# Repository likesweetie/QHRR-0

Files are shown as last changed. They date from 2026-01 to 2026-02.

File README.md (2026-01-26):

# !!직접 main 브랜치에 작업하지 않습니다!! 
## 아래 과정에서 에러난다고 GPT한테 물어봐서 Reset / Force Push같은거 하면 넌 뒤짐
잔디에 에러 스샷 올려서 같이 고민하기

### 작업 → Commit → Push 순서

1. 코드 수정 or 파일추가

2. GitHub Desktop에서 변경 사항 확인

3. Summary에 작업 내용 요약 작성

4. Commit to [branch 이름] (없으면 적당히 branch 생성)

5. Push origin

6. Push 후 GitHub 웹 페이지에서 Pull Request(PR) 생성 -> 관리자가 리뷰 승인 후 병합

### 사전설정

#### GitHub Desktop 설치 및 초기세팅

1. 아래 공식 링크에서 GitHub Desktop을 다운로드합니다.
👉 https://desktop.github.com/

2. 설치 후 실행합니다.

3. 실행 시 GitHub 로그인을 요청하면 본인의 GitHub 계정으로 로그인합니다

4. GitHub Desktop 실행

5. 상단 메뉴에서 File → Clone repository…

6. URL 탭 선택, 저장소 주소 입력

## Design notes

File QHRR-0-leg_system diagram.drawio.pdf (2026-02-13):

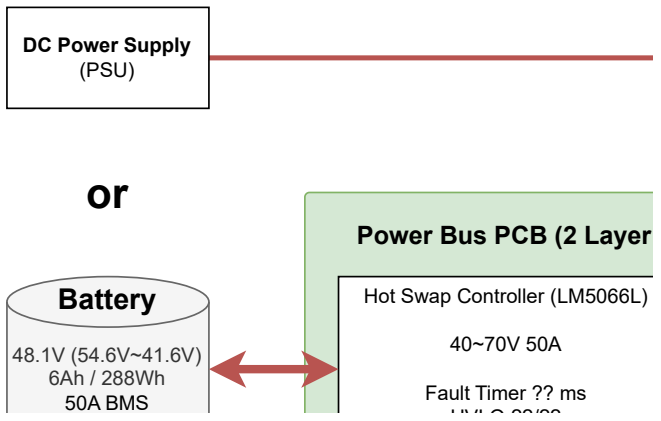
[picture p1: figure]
48.1V (54.6V~41.6V) 6Ah / 288Wh 50A BMS; Hot Swap Controller (LM5066L); Fault Timer ?? ms UVLO ??/??; Battery; Power Bus PCB (2 Layer; DC Power Supply (PSU)

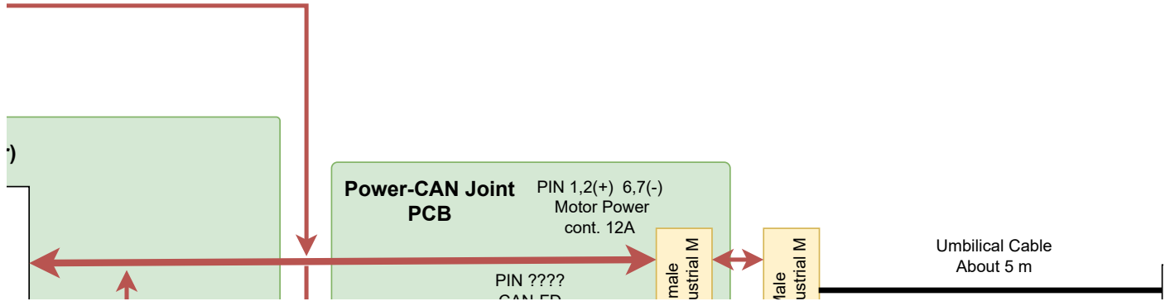
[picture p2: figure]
ustrial M; Male; male; PIN 1,2(+) 6,7(-) Motor Power cont. 12A; PIN ???? CAN FD; Power-CAN Joint PCB; Umbilical Cable About 5 m
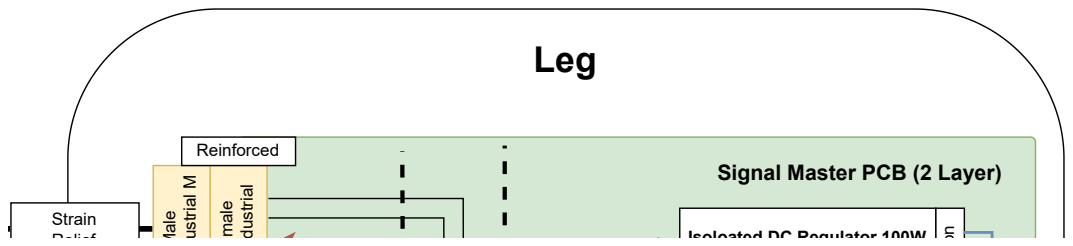
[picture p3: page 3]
Leg; male; dustrial; ustrial M; Male; Reinforced; Strain Relief

Signal Master PCB (2 Layer)

Isoloated DC Regulator 100W

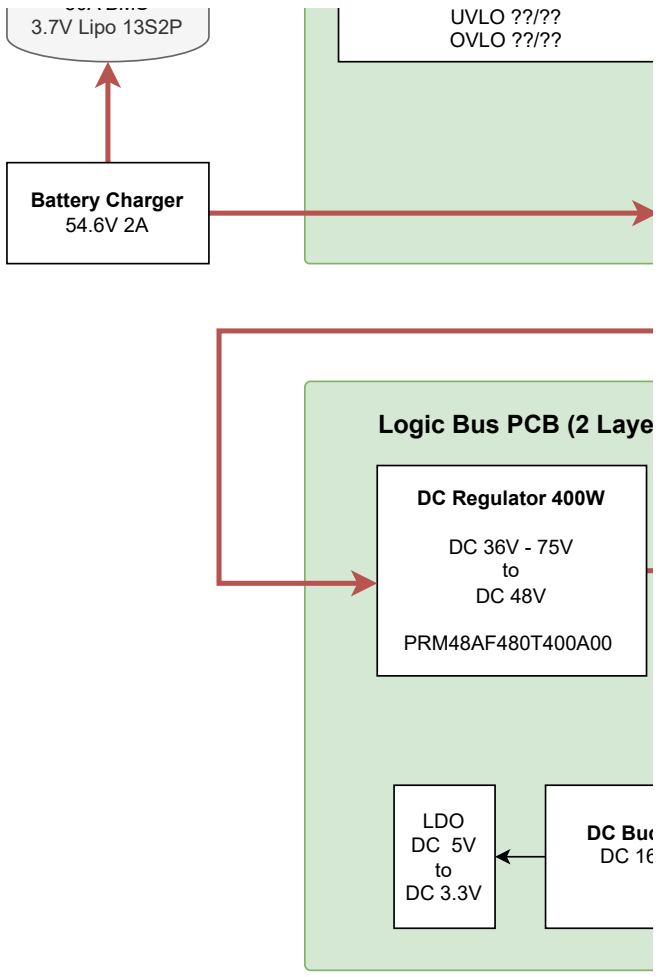
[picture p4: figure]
50A BMS 3.7V Lipo 13S2P; DC Regulator 400W; PRM48AF480T400A00; UVLO ??/?? OVLO ??/??; Battery Charger 54.6V 2A; Logic Bus PCB (2 Laye; DC Buc DC 16; LDO DC 5V to DC 3.3V

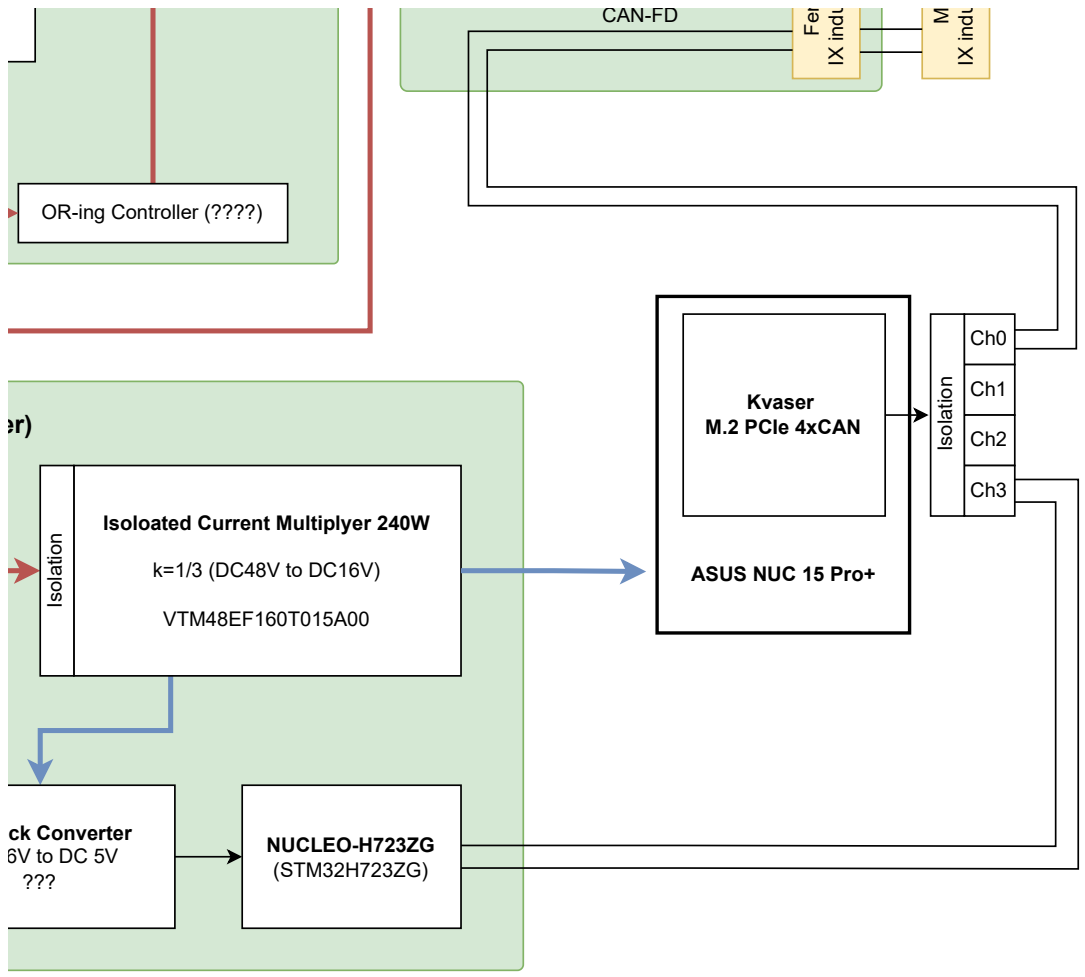
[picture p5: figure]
Isoloated Current Multiplyer 240W; VTM48EF160T015A00; NUCLEO-H723ZG (STM32H723ZG); OR-ing Controller (????) Isolation; IX indu; Fem; CAN-FD; ASUS NUC 15 Pro+; Isolation; Kvaser M.2 PCIe 4xCAN; ck Converter 6V to DC 5V ???
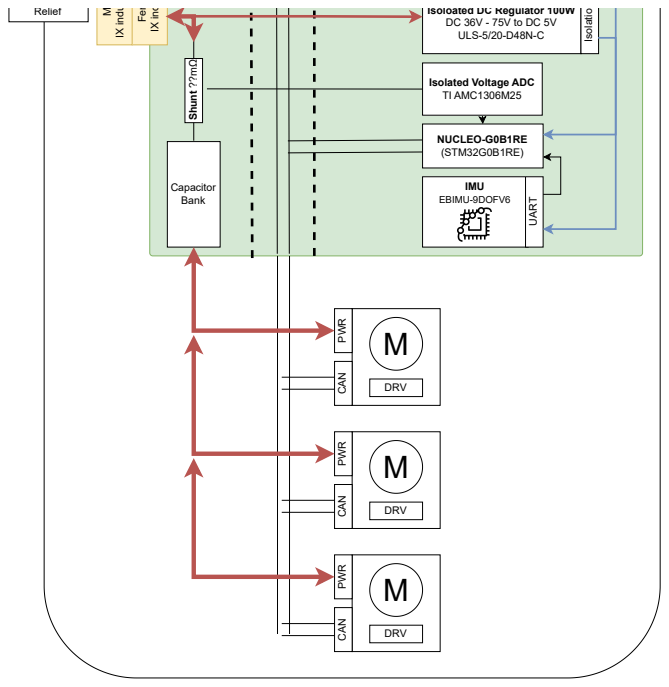
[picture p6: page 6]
DRV; CAN; NUCLEO-G0B1RE (STM32G0B1RE); IMU EBIMU-9DOFV6; UAR; Capacitor Bank; IX ind; Fem; Isolatio; Shunt ??mΩ; IX indu; Relief

Isoloated DC Regulator 100W
ULS-5/20-D48N-C

Isolated Voltage ADC
TI AMC1306M25

PWR CAN PWR CAN PWR

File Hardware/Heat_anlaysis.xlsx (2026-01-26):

 | Stack | 두께 m | 접촉면적 m^2 | 열저항 | 열전도율 W/(m·K) | 발열(W)
Ambient Temp. (C)
30
Max surface Temp
50 | 알루미늄 7075 외피(Fin) | 0.005 |  | 0.0078125 | 128 | 0
 | 알루미늄 7075 외피(구조물) | 0.005 |  | 0.0078125 | 128 | 0
 | 서멀그리스 |  |  | 0.125 | 8 | 0
 | 구리 T2 Heat Sink | 0.01 |  | 0.002493765586 | 401 | 0
 | 서멀그리스 |  |  | 0.125 | 8 | 0
 | CPU (cTDP / 기본65W) |  |  |  |  | 65

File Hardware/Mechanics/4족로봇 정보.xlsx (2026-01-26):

 | standing 크기 | 무게 | 가반하중 | 최대속도 |  | Thigh | calf
RBQ10 | 945 X 440 X 565mm | 37kg | 10kg | 7.2km/h | 2m/s | 1.8kg | 0.45kg
B2 | 1098 X 450 X 645 mm | 60kg | 120kg | 21.6km/h | 6m/s | 4.536kg | 0.404kg
spot | 1100 X 500 X 610 mm | 32.7kg | ? | 5.76km/h | 1.6m/s | 2.256kg | 0.330kg
Black panther 2 | ? X ? X 630 mm | 38kg | ? | 36km/h | 10m/s
ANYmal | 930 X 530 X 890 mm | 50kg | 15kg | 4.69km/h | 1.30m/s
Ghost Robotics vision 60 | ? X ? X ? Mm | 51kg | 10kg | 10.8km/h | 3m/s | 1.2kg | 0.38kg
 |  |  |  |  |  |  |  | hip
 |  |  |  |  |  |  |  | 2.75kg

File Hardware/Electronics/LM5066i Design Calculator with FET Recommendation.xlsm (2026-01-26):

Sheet: Instructions
 |  |  |  |  | © 2014
 | LM5066/I Design Tool with FET Recommendation - Rev. A
 | Typical design procedure
 | Before proceeding, please go through the application note |  |  | Robust Hot Swap Design (https://www.ti.com/lit/an/slva673a/slva673a.pdf)
 | and the design example in the |  | LM5066I Datasheet (See "Applications and Implementation") (https://www.ti.com/lit/ds/symlink/lm5066i.pdf)
Step 1: | 1. Enter your system parameters (operating voltage limits, load current, load capacitance, system max ambient temperature )
 | 2. Enter FET operating parameters (preferred FET operating junction temperature, thermal impedance)
 |  | Note: The tool adjusts the number of FETs required in parallel to maintain the preferred FET operating junction temperature.
 |  | Note: Thermal impedance is heavily dependent on the board layout and the amount of copper connected to the drain of the FET.
 |  | Thermal impedance is required to determine MOSFET SOA margin.
 | 3. Enter the load startup conditions (startup mode, startup load type, load turn on threshold, startup load value)
Step 2: | 1. Set the current limit settings. Use a resistive divider to reduce effective sense resistance if needed.
 | 2. Select Target power limit greater than the Minimum Recommended Power Limit threshold
Step 3: | 1. Select MOSFETs from the dropdown menu.
 | 2. Compare their SOA margin, cost, power dissipation at full load and number of FETs required in parallel to know which FET fits your design perfectly.
 |  | Note: You can also enter the SOA data of a non-TI FET to compare it with TI FETs.
 |  | An SOA margin greater than 1.1 is required and greater than 1.3 is recommended for safe operation
 | 3. If none of the FETs satisfy the SOA margin, try to change the following parameters:
 |  | a. In case of power limit startup mode, reduce the load startup conditions or use a different FET in the non-TI FET column.
 |  | b. In case of soft start startup mode, reduce the fault timer or use a different FET in the non-TI FET column.
 | Note: The FETs selected in this section will be available as the final choices in the next section.
 | (Links to the TI FET product pages have been provided)
Step 4: | 1. Select an FET from the dropdown menu.
 | 2. Review start up conditions to check whether selected FET is operating with reasonable margin, within the SOA curve.
 | 3. Adjust Soft-start and Timer capacitances to get accurate SOA measurements.
Step 5: | 1. Enter desired UVLO and OVLO threshold values to get recommended resistor values.
 | 2. In case any of the cells in the threshold table is highlighted in red, adjust the resistor values.
 | 3. If nearest resistor values still give red highlighted cells, change the configuration
Step 6: | Done. View the design summary with all the results
 | * Comments on the data to be filled/expected are provided to guide you
 | Notes
 | 1. This worksheet is designed for use with Microsoft Excel 5.0 or later. Its use is intended to assist power supply designers in their
 | routine, day-to-day calculations.
 | 2. All worksheets have light green inputs cells, white calculated cells, yellow warning cells and red high-risk cells.
 | 3. Formulas and device constants used in the spreadsheet are locked to prohibit them from accidentally being overwritten or deleted.
 | TEXAS INSTRUMENTS TEXT FILE LICENSE Copyright (c) 2014 Texas Instruments Incorporated All rights reserved not granted herein. Limited License. Texas Instruments Incorporated grants a world-wide, royalty-free, non-exclusive license under copyrights and patents it now or hereafter owns or controls to make, have made, use, import, offer to sell and sell ("Utilize") this software subject to the terms herein. With respect to the foregoing patent license, such license is granted solely to the extent that any such patent is necessary to Utilize the software alone. The patent license shall not apply to any combinations which include this software, other than combinations with devices manufactured by or for TI (“TI Devices”). No hardware patent is licensed hereunder. Redistributions must preserve existing copyright notices and reproduce this license (including the above copyright notice and the disclaimer and (if applicable) source code license limitations below) in the documentation and/or other materials provided with the distribution Redistribution and use in binary form, without modification, are permitted provided that the following conditions are met: * No reverse engineering, decompilation, or disassembly of this software is permitted with respect to any software provided in binary form. * any redistribution and use are licensed by TI for use only with TI Devices. * Nothing shall obligate TI to provide you with source code for the software licensed and provided to you in obje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

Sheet: Design Calculator
LM5066/I PMBus Hot Swap Design Tool with FET Recommendation
 | www.ti.com/hotswap
 |  |  | Enter Values in Green Shaded Cells
 |  |  | Calculated Values are shown in White Cells
 |  |  | Yellow and Red cells highlight potential issues with the design. Red highlights items that are higher risk.
 |  |  | LM5066I Datasheet (http://www.ti.com/product/lm5066i)
 |  |  | *For additional questions not addressed in the instructions, please post on E2E.ti.com
 | Step 1: System Parameters |  |  | Minimum Input Operating Voltage: VIN(MIN) | 40 | V
 |  |  |  | Nominal Input Operating Voltage: VIN(NOM) | 48 | V
 |  |  |  | Maximum Input Operating Voltage: VIN(MAX) | 70 | V
 |  |  |  | Maximum Load Current: IOUT(MAX) | 50 | A
 |  |  |  | Maximum Output Load Capacitance: CLOAD | 220000 | µF
 |  |  |  | Maximum Ambient Operating Temperature: TMAX | 50 | oC | Note: The tool adjusts the number of FETs required in parallel to maintain the preferred FET operating junction temperature (TJ,DC)
 |  |  |  | Preferred FET Operating Junction Temperature (TJ,DC) | 80
 |  |  |  | Estimated MOSFET RQJA | 100
 |  |  |  | Load Turn-On Threshold | 40 | V
 |  |  |  | Startup Load Type | Constant Current |  | Note: In case none of the FETs satisfy the SOA margin, reduce the load startup conditions
 |  |  |  | Startup Load Value | 10 | A
 |  |  |  | System start-up mode | Soft Start |  | Note: In case none of the FETs satisfy the SOA margin, reduce the fault timer
 |  |  |  | Fault timer required | 0.050 | ms
 | Step 2: Current Limit and Power Limit Selection |  |  | Current Limit Range (CL) | 26 mV
 |  |  |  | Maximum Recommended Value for Effective Sense Resistance | 0.46 | mW
 |  |  |  | Use External Resistor Divider to Reduce Effecitve RS | No
 |  |  |  | Enter the Resistance for RS | 0.1 | mW
 |  |  |  | Recommended Value for RCL1 | NA | W
 |  |  |  | Recommended Value for RCL2 | NA | W
 |  |  |  | Enter value for RCL1 | 10 | W
 |  |  |  | Enter value for RCL2 | 2.8 | W
 |  |  |  | Effective Sense Resistance (RS,EFF) | 0.10 | mW
 |  |  |  | Resulting Minimum Current Limit | 234.0 | A
 |  |  |  | Resulting Typical Current Limit | 260.0 | A
 |  |  |  | Resulting Maximum Current Limit | 286.0 | A
 |  |  |  | Maximum Power Dissipation in RS | 8.2 | W
 |  |  |  | Fault Response | Latch Off |  |  |  |  |  | Note: Use a resistive divider to fine tune the current limit setting if needed
 |  |  |  | Circuit Breaker to Current Limit Raitio | 1.9 x Current Limit
 |  |  |  | Minimum Power Limit to Ensure Vsns > 4mV (PLIM,MIN) | 2800.0 | W
 |  |  |  | Target Power Limit | 3000.00 | W
 |  |  |  | Calculated RPWR | 36.71 | kW
 |  |  |  | Actual RPWR | 47 | kW
 |  |  |  | Actual PLIM | 3720.00 | W
 | Step 3: MOSFET Suggestions |  |  | Q1 FET Name | Part Number , SOA margin , $1ku | Part Number , SOA margin , $1ku | MOSFET from Non-TI Suppliers
 | Scroll down the dropdown menu to select MOSFET |  |  | Choose FETs for comparison | CSD19536KTT , 1.23 , $1.972 | CSD19535KTT , 1.16 , $1.313 | Non-TI MOSFET
 |  |  |  | MOSFET On resistance @ TJ,DC | 3.144 | 4.794 | 2.000
 |  |  |  | Maximum FET Junction Temperature | 175 | 175 | 175 | mW
 |  |  |  | 10ms SOA Current@ VIN(MAX) | 400.00 | 400.00 | 400.00 | oC
 |  |  |  | 100µs SOA Current @ VIN(MAX) | 102.96 | 37.38 | 100.00 | A
 |  |  |  | 1ms SOA Current @ VIN(MAX) | 9.39 | 4.99 | 20.00 | A
 |  |  |  | 10ms Current at @ VIN(MAX) | 2.92 | 1.49 | 5.00 | A
 |  |  |  | 100ms SOA Current at @ VIN(MAX) | 1.49 | 0.87 | 1.00 | A
 |  |  |  |  |  |  |  | A
 | Note: TI recommends choosing a FET with SOA current specified for 100ms and/or 1s or DC. If choosing a FET without these parameters, this calculator will estimate the values via extrapolation, which leaves an inherent associated risk. |  |  | Number of FETs suggested | 6 | 7 | 5
 |  |  |  | FET Power dissapation at full load (per FET) | 0.22 | 0.24 | 0.20 | #
 |  |  |  | Maximum steady state FET Junction Temperature (TJ,DC) | 71.83 | 74.46 | 70.00 | W
 |  |  |  | SOA Margin | 2.01 | 0.96 | 2.00 | oC
 |  |  |  | Webpage Link | CSD19536KTT | CSD19535KTT | Enter Webpage Link
 |  |  |  | Cost per FET (1k USD) | $1.972 | $1.313 | Enter Cost Details |  |  | Note: Hover here to see the 3 values affecting this curve, consult a thermal expert if you are unsure!
 |  |  |  | Total Cost of the FETs | $11.832 | $9.191
 |  |  |  |  | Note: If none of the FETs are meeting the requirement, reduce the startup load or select a stronger FET in cell H54
 |  |  |  |  | Note: If none of the FETs are meeting the requirement, reduce the fault timer or select a stronger FET in cell H54
 | Step 4: Startup |  |  | Select preferred FET from the dropdown menu | CSD19536KTT , 2.63 , $1.972
 |  |  |  | Timer Overview
 |  |  |  | Typical Start Time with Vinmax (Tstart) | 350.00 | ms
 |  |  |  | IFET - ILOAD margin (lowest for Vout range) | 81.48148148%
 |  |  |  | Target Fault Timer: Tstart + Margin | 525.00 | ms
 |  |  |  | Target Timer capacitance | 10096.15 | nF
 |  |  |  | Selected Timer capacitance | 100 | nF
 |  |  |  | Final Fault Timer(Tfault) | 5.20 | ms
 |  |  |  | Derated SOA / PLIM | #N/A
 |  |  |  | Can a "hot" board be hotplugged | No
 |  |  |  | Recommended slew Rate (max) | #N/A | V/ms
 | Note: This is the typical dv/dt rate, but max value can be 2x. This is because the gate source current can vary from 20uA to 40uA. Thus TI recommends keeping the overall SOA margin during start-up >1.5 in order to compensate for this. |  |  | Recommended slew Rate (min) | #N/A | V/ms
 |  |  |  | dv/dt rate on Vout | 0.2 | V/ms
 |  |  |  | calculated SS capacitance | 100.00 | nF
 |  |  |  | actual SS capacitance | 100 | nF
 |  |  |  | actual typical dv/dt rate on Vout | 0.20 | V/ms
 |  |  |  | SOA margin during start-up | #N/A
 |  |  |  | Target Fault Time | 0.01 | ms
 |  |  |  | Calculated Timer Capacitance | 0.19 | nF
 |  |  |  | Actual Timer Capacitance ( pick one smaller than CT,CALC) | 4.7 | nF
 |  |  |  | Actual Fault Time (Tfault) | 0.24 | ms
 |  |  |  | SOA margin during "hot-short" or "start-into short" | #N/A
 |  |  |  | Resulting Typical Insertion Delay Time | 3.81875 | ms
 |  |  |  | Resulting Typical Restart Time | 38.95 | ms
 | Step 5: UVLO, OVLO & PGD Thresholds |  |  | Select Option A or Option B | Option B
 |  |  |  | Desired Upper UVLO Threshold | 38 | V
 |  |  |  | Desired Lower UVLO Threshold | 35 | V
 |  |  |  | Desired Upper OVLO Threshold | 65 | V
 |  |  |  | Desired Lower OVLO Threshold | 63 | V
 |  |  |  | Recommended Resistance for: R1 | 150.00 | kW
 |  |  |  | R2 | 11.44 | kW
 |  |  |  | R3 | 95.24 | kW
 |  |  |  | R4 | 3.75 | kW
 |  |  |  | Enter the Resistance for R1 | 150 | kW
 |  |  |  | Enter the Resistance for R2 | 11.5 | kW
 |  |  |  | Enter the Resistance for R3 | 95.3 | kW
 |  |  |  | Enter the Resistance for R4 | 3.74 | kW
 |  | Resulting Thresholds: | Minimum | Typical | Maximum
 |  | Resulting Upper UVLO Threshold = | 36.24 | 37.83 | 39.41 | V
 |  | Resulting Lower UVLO Threshold = | 33.84 | 34.83 | 35.81 | V
 |  | Resulting Upper OVLO Threshold = | 63.29 | 65.14 | 67.00 | V
 |  | Resulting Lower OVLO Threshold = | 61.00 | 63.14 | 65.47 | V
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

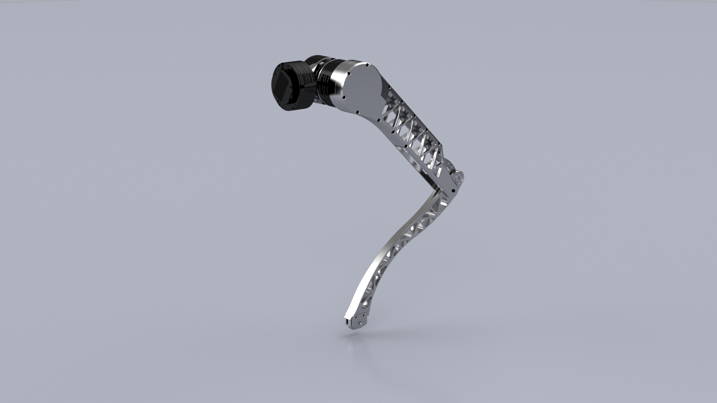
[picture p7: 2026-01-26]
Hardware/Mechanics/Untitled Project.jpg

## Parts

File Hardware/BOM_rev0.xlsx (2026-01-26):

 |  |  |  |  |  |  |  |  |  |  | 총액 | ₩4096015
 |  |  |  |  |  |  |  |  |  |  | 1순위 총액 | ₩3685553
Part Number | Rev | Class | Type | Retail | Priority | Part Name | Part Description | Qty. | Spec / Model | Manufacturer | Supplier | Price/Qty | Price | 서류처리? | 구매? | 구분
 | 0 | Electronics | Component | TRUE | 1 | ASUS NUC 15 Pro+ NUC15CRSU9 (베어본) | Control PC | 1 |  | ASUS |  | ₩1400000 | ₩1400000 | 구매기안중 |  | SPG RISE 재료비
 | 0 | Electronics | Component | TRUE | 1 | 삼성전자 노트북 램 DDR5- 32GB | Control PC | 1 |  | 삼성전자 |  | ₩350000 | ₩350000 | 구매기안중 |  | SPG RISE 재료비
 | 0 | Electronics | Component | TRUE | 1 | m.2 SSD 1TB 2280 | Control PC | 1 |  | 하이닉스 |  | ₩400000 | ₩400000 | 구매기안중 |  | SPG RISE 재료비
 | 0 | Electronics | Component | TRUE | 1 | Kvaser M.2 PCIe 4xCAN | CAN | 1 |  | KVASER |  | ₩770000 | ₩770000 | 구매기안중 |  | SPG RISE 재료비
 |  | Electronics | Component | TRUE | 1 | EBIMU-9DOFV6 | IMU | 1 |  | 이투박스 | 디바이스마트 | ₩173800 | ₩173800 |  |  | SPG RISE 재료비
 |  | Electronics | Component | TRUE | 1 | NUCLEO-G0B1RE | MCU | 1 |  | STMicroelectronics | 디바이스마트 | ₩21230 | ₩21230 |  |  | SPG RISE 재료비
 |  | Electronics | Component | TRUE | 1 | ULS-5/20-D48N-C | DC/DC 컨버터 | 1 |  |  | 디바이스마트 | ₩77539 | ₩77539 |  |  | SPG RISE 재료비
 |  | Electronics | Component | TRUE | 1 | PVHC7F23SS644 SWITCH PUSHBUTTON SPST 20A 250V | 전원스위치 | 1 | 20A 250V | E-Switch | 디바이스마트 | ₩47652 | ₩47652 |  |  | SPG RISE 재료비
 |  | Electronics | Component | TRUE | 1 | AMC1306M25QDWVRQ1 | ADC 컨버터 | 5 |  | Murata Power | 디바이스마트 | ₩10593 | ₩52965 |  |  | SPG RISE 재료비
 |  | Electronics | Component | TRUE | 1 | WSLP59311L000FEB 션트저항 1m옴 | 션트저항 | 2 |  | Vishay Dale | 디바이스마트 | ₩5731 | ₩11462
 |  | Electronics | Component | TRUE | 1 | WSLP5931L1000FEA 션트저항 0.1m옴 | 션트저항 | 2 |  | Vishay Dale | 디바이스마트 | ₩6347 | ₩12694 |  |  | SPG RISE 재료비
 |  | Electronics | Component | TRUE | 1 | B380-13-F | 쇼트키 다이오드 | 5 |  | Diodes Incorporated | 디바이스마트 | ₩1595 | ₩7975 |  |  | SPG RISE 재료비
 |  | Electronics | Component | TRUE | 1 | 1N4148W-7-F | 스위칭다이오드 | 10 |  | Diodes Incorporated | 디바이스마트 | ₩198 | ₩1980 |  |  | SPG RISE 재료비
 |  | Electronics | Component | TRUE | 1 | CSD19536KTT | 배터리 전원 FET | 10 |  | TI | 디바이스마트 | ₩9922 | ₩99220 |  |  | SPG RISE 재료비
 |  | Electronics | Component | TRUE | 1 | MMBT3904 | BJT TR | 20 |  | Diotec Semiconductor | 디바이스마트 | ₩187 | ₩3740 |  |  | SPG RISE 재료비
 |  | Electronics | Component | TRUE | 1 | 5.0SMDJ43CAS | ESD 다이오드 69.4VC | 10 |  | Littelfuse Inc. | 디바이스마트 | ₩3938 | ₩39380 |  |  | SPG RISE 재료비
 |  | Electronics | Component | TRUE | 1 | SSW-138-01-T-S | 신호 커넥터 | 4 |  | Samtec | 디바이스마트 | ₩5742 | ₩22968 |  |  | SPG RISE 재료비
 |  | Electronics | Component | TRUE | 1 | XT60PW-M | 전원 커넥터 | 10 |  | Changzhou Amass Elec | 디바이스마트 | ₩1089 | ₩10890 |  |  | SPG RISE 재료비
 |  | Electronics | Component | TRUE | 1 | Male 플러그 4핀 [LP-16-C04PE-02-001] | 전원 커넥터 | 4 |  | crinco | 디바이스마트 | ₩7040 | ₩28160 |  |  | SPG RISE 재료비
 |  | Electronics | Component | TRUE | 1 | Female 원형 소켓 4핀 [LP-16-J04SX-02-101] | 전원 커넥터 | 4 |  | crinco | 디바이스마트 | ₩5280 | ₩21120 |  |  | SPG RISE 재료비
 |  | Electronics | Component | TRUE | 1 | 2311765-1 | 신호 커넥터 | 2 |  | TE Connectivity | 디바이스마트 | ₩4169 | ₩8338
 |  | Electronics | Component | TRUE | 2 | PRM48AF480T400A00 | DC/DC 컨버터 | 1 |  | Vicor | 디바이스마트 | ₩226072 | ₩226072 |  |  | SPG RISE 재료비
 |  | Electronics | Component | TRUE | 2 | VTM48EF160T015A00 | DC/DC 컨버터 | 1 |  | Vicor | 디바이스마트 | ₩130520 | ₩130520
 |  | Electronics | Component | TRUE | 2 | NUCLEO-H723ZG | MCU | 1 |  | STMicroelectronics | 디바이스마트 | ₩53870 | ₩53870
 |  | Mechanical | Component | TRUE | 1 | C-NUHFN160 | 손잡이 | 5 |  |  | 미스미 | ₩8888 | ₩44440 |  |  | 태성 RISE 재료비
 |  | Mechanical | Component | TRUE | 1 | 쉬멕스 풀림방지 볼트 M3 50pcs | 볼트 | 1 |  | 쉬멕스 | 쉬멕스 | ₩40000 | ₩40000
 |  | Mechanical | Component | TRUE | 1 | 쉬멕스 풀림방지 볼트 M4 50pcs | 볼트 | 1 |  | 쉬멕스 | 쉬멕스 | ₩40000 | ₩40000
 |  | Mechanical | Component | TRUE | 1 | 핀 | 위치 핀 | 10 |  | 미스미 | 미스미
 |  |  |  |  |  |  |  |  |  |  |  |  | ₩0
 |  |  |  |  |  | 각종 FC에 사용하는 GH1.25 |  |  |  |  |  |  | ₩0
 |  |  |  |  |  |  |  |  |  |  |  |  | ₩0
 |  |  |  |  |  |  |  |  |  |  |  |  | ₩0
 |  | Software
S-01 | 0 | SQLite
 |  | OpenBOM
 |  | WireViz
 |  | ZeroMQ |  |  |  | 원격 메시징 라이브러리 |  |  |  | JCL PCB
 |  | googletest
 |  |  |  | FALSE |  | Heat Sink

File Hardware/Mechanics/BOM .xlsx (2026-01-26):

 |  |  |  |  | (단위 : 천원)
 | 구매처 | 품번/이름 | 수량 | 재료 | 업체명 : 유일 | 엠더블유에스 | GP KOREA | 지엔피
가공 부품 |  | calf_link_I | 1 | S45C | 120 | 95 | 60 | 30
 |  | calf_link_II | 1 | S45C | 150 | 75 | 60 | 30
 |  | calf_thigh_I | 1 | S45C | 80 | 70 | 60 | 35
 |  | connector_1 | 1 | 6061-T6 | 80 | 80 | 80 | 55
 |  | connector_2 | 1 | 6061-T6 | 90 | 90 | 80 | 60
 |  | foot_cover_1 | 1 | 6061-T6 | 50 | 120 | 60 | 40
 |  | foot_cover_2 | 1 | 6061-T6 | 50 | 120 | 60 | 40
 |  | hip_calf_jig | 1 | 6061-T6 | 180 | 420 | 150 | 90
 |  | hip_stopper | 1 | 7075-T6 | 220 | 180 | 120 | 45
 |  | hip_thigh_2 | 1 | 6061-T6 | 350 | 500 | 200 | 150
 |  | link | 1 | S45C | 400 | 260 | 250 | 250
 |  | shaft_1 | 1 | S45C | 120 | 85 | 60 | 40
 |  | shaft_2 | 1 | S45C | 200 | 80 | 80 | 60
 |  | thigh(1)-2 | 1 | 6061-T6 | 350 | 580 | 550 | 350
 |  | thigh(2)-2 | 1 | 6061-T6 | 350 | 580 | 550 | 350
 |  | thigh_stopper | 1 | 7075-T6 | 150 | 150 | 100 | 45
 |  | spacer_3.5 | 2 | 6061-T6 | 80 | 50 | 120 | 40
 |  | calf | 1 | 7075-T6 | 400 | 650 | 450 | 320
 |  |  |  | 총 가격 : | 3420 | 4185 | 3090 | 2030
 |  |  |  | 세금 포함 | 약 3,760,000 | 약 4,603,000 | 약 3,399,000 | 약 2,233,000
베어링
 | NSK | 6900ZZ(C-E6900) | 2 |  | 내경 : 10 |  | 외경 : 22
볼트 | NSK | 6001ZZ(C-E6001) | 2 |  | 내경 : 12 |  | 외경 : 28
 | NTN | C-E678ZZ | 2 |  | 내경 : 6 |  | 외경 : 10
핀
스페이서 | 쉬멕스 | P00180-04-10 | 50 |  | M4 볼트 |  | 길이 10mm
 | 쉬멕스 | P00180-04-16 | 50 |  | M4 볼트 |  | 길이 16mm
 | 미스미 | E-FPDSC4-P3-L4-B4 | 7
 | 미스미 | CLBP12-16-10-UKC | 1 | 5000계 알루미늄 합금
 |  | CLBP10-13-3-UKC | 2 | 5000계 알루미늄 합금

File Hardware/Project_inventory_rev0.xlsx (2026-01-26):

Part Number | Rev | Part Name | Class | Part Description | Qty. | Spec / Model | Supplier | Price/Qty | Price
EL-01 | 1 | NUC | Electronics | Control PC

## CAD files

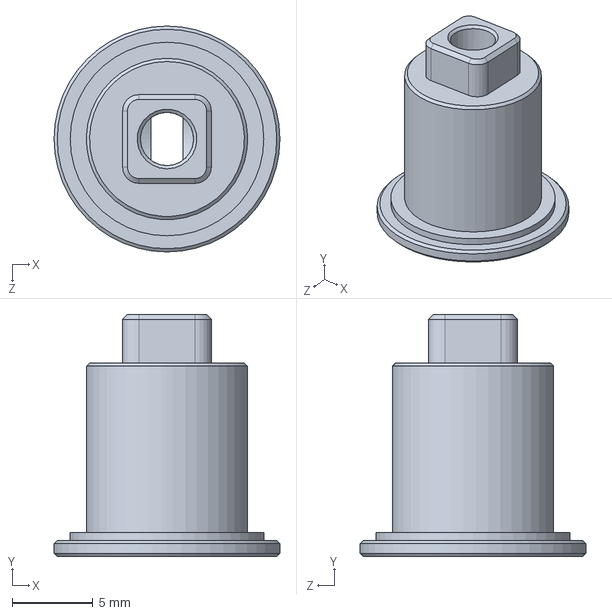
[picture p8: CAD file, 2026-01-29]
Hardware/Mechanics/4족 3D/calf_link_l.SLDPRT
14.0 x 15.0 x 14.0 mm

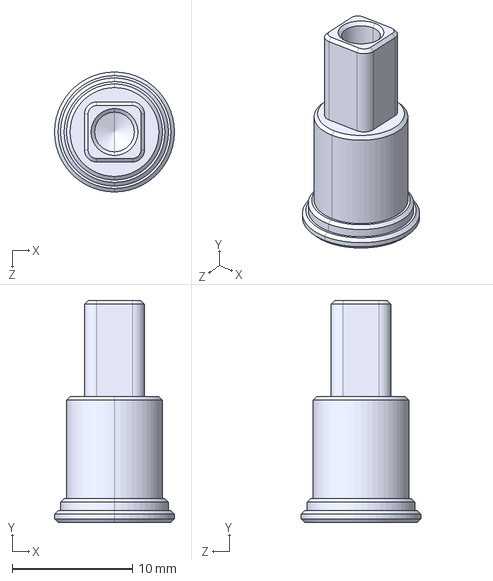
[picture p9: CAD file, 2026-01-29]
Hardware/Mechanics/4족 3D/STEP 파일/shaft_1.STEP
10.0 x 18.5 x 10.0 mm

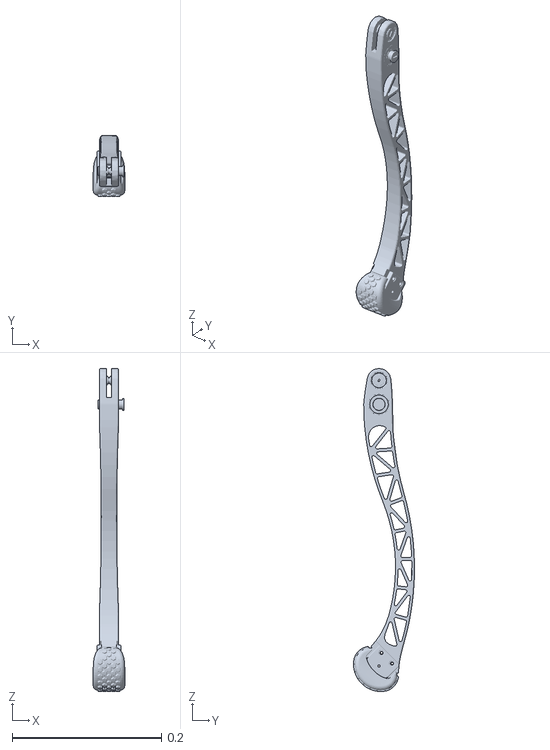
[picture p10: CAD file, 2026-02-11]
Hardware/Mechanics/4족 3D/URDF_14/meshes/Calf_link.STL
0.0423 x 0.0816 x 0.432

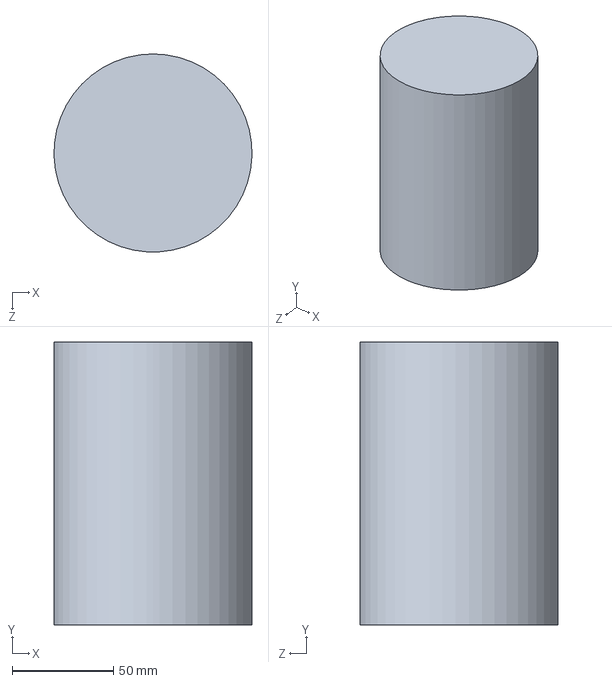
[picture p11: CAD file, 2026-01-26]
Hardware/Mechanics/시뮬/Thigh_calf_motor.SLDPRT
97.9 x 140.0 x 98.0 mm

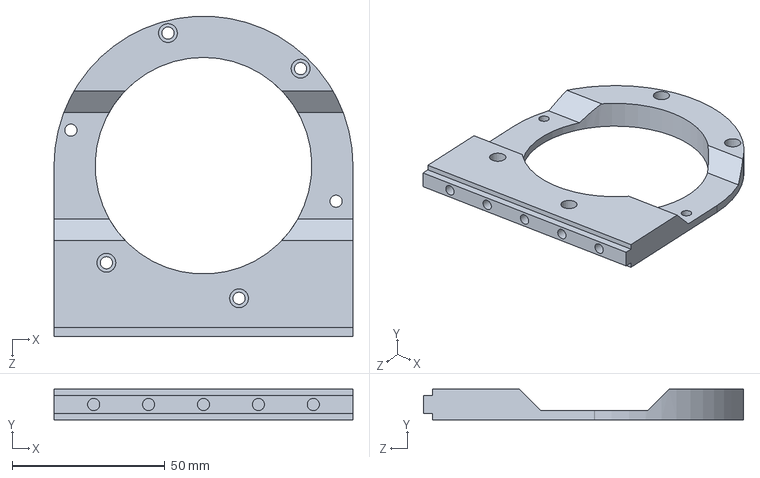
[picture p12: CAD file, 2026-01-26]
Hardware/Mechanics/안 쓰는 것/hip-thigh.SLDPRT
98.0 x 10.0 x 104.9 mm

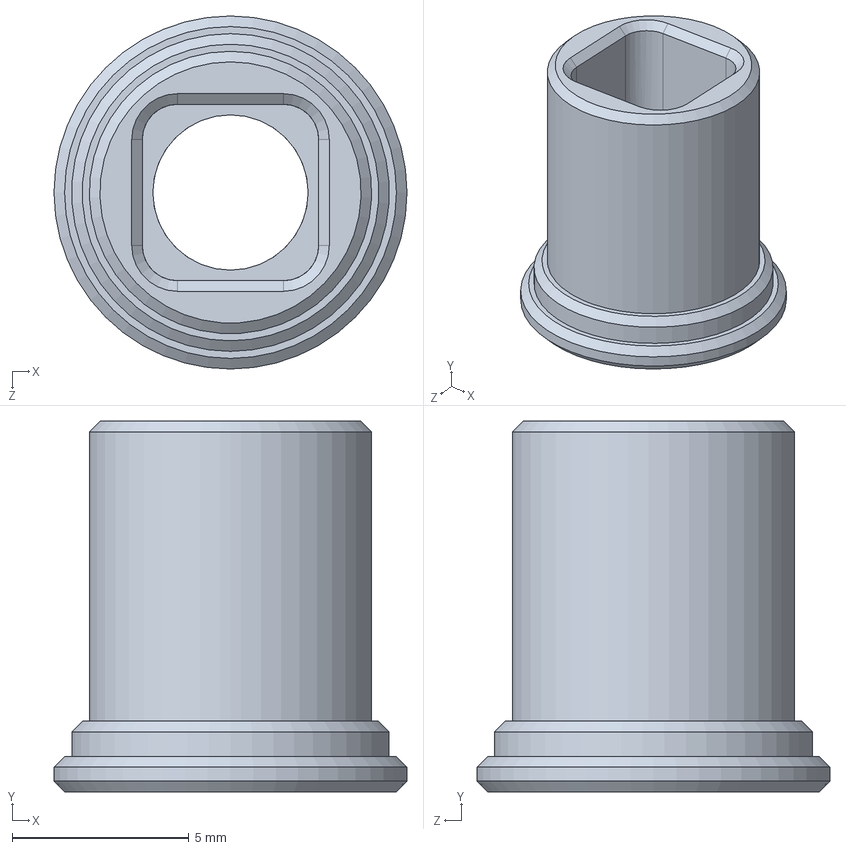
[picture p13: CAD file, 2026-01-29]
Hardware/Mechanics/4족 3D/shaft_2.SLDPRT
10.0 x 10.5 x 10.0 mm

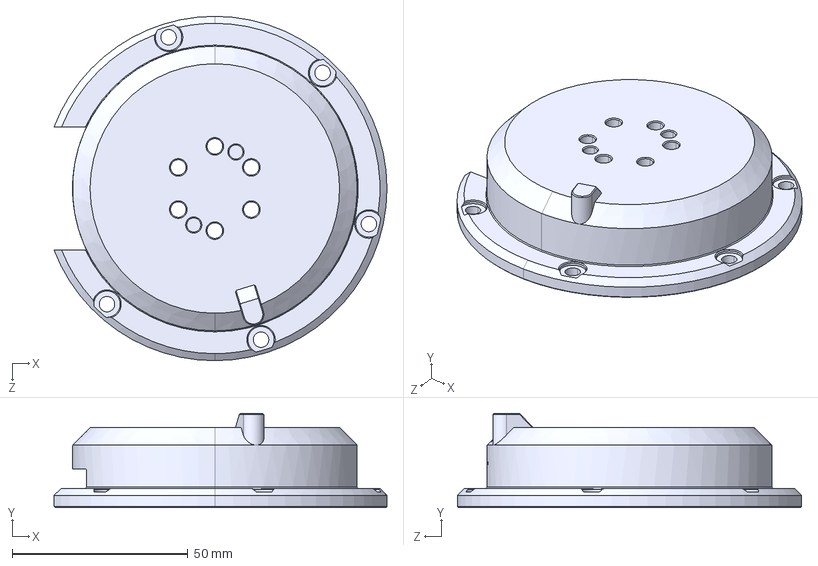
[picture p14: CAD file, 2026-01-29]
Hardware/Mechanics/4족 3D/STEP 파일/hip_calf_jig_2.STEP
94.8 x 26.8 x 98.0 mm

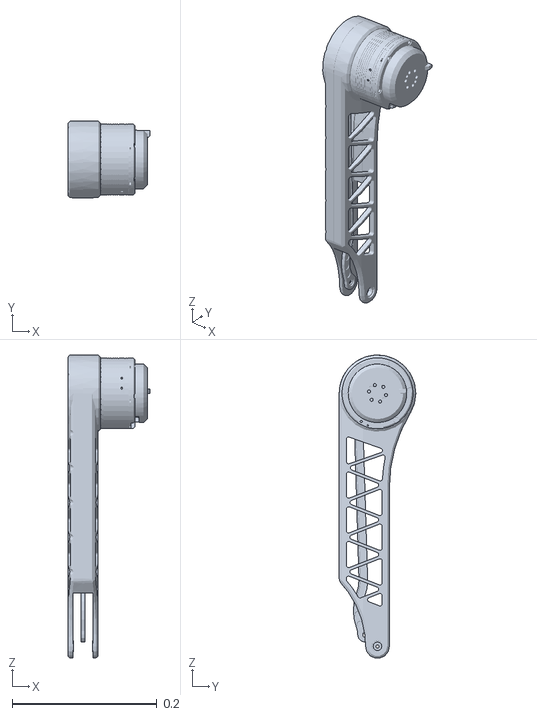
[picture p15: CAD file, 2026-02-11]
Hardware/Mechanics/4족 3D/URDF_14/meshes/Thigh_link.STL
0.114 x 0.106 x 0.419

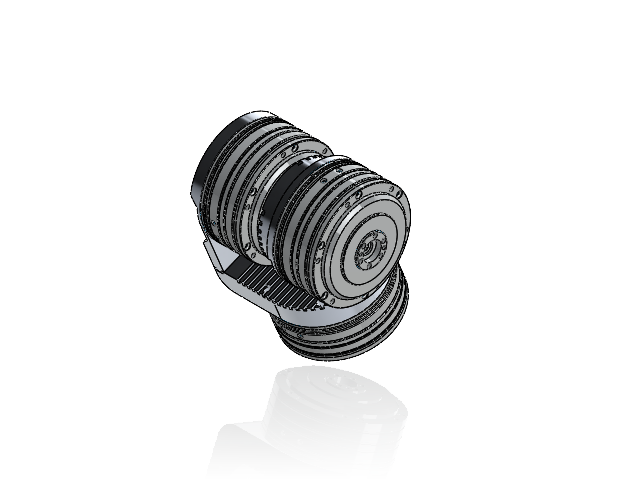
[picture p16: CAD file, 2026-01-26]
Hardware/Mechanics/안 쓰는 것/hip_thigh assembly.SLDASM
AK10-9 KV60 V3.0-3D.step x 3
hip_calf_jig
hip_jig
hip-thigh

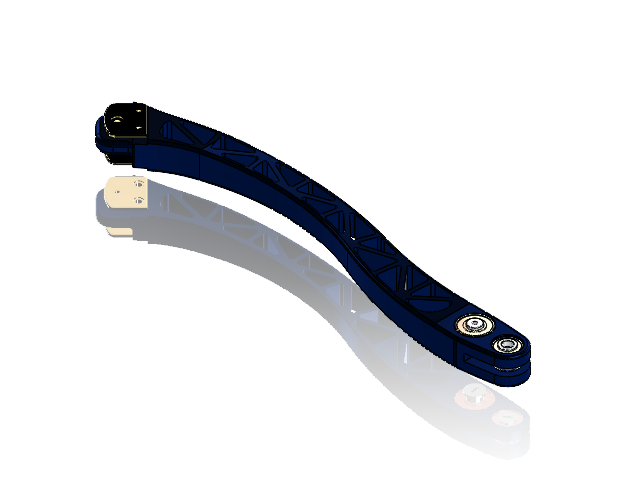
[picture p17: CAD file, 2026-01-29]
Hardware/Mechanics/4족 3D/Calf_link.SLDASM
B6001ZZ x 2
B6900ZZ x 2
calf_link_l
calf_link_ll
calf_thigh_I
calf-1
foot_cover_1
foot_cover_2
CLBP10-13-3-UKC x 2
CLBP12-16-10-UKC

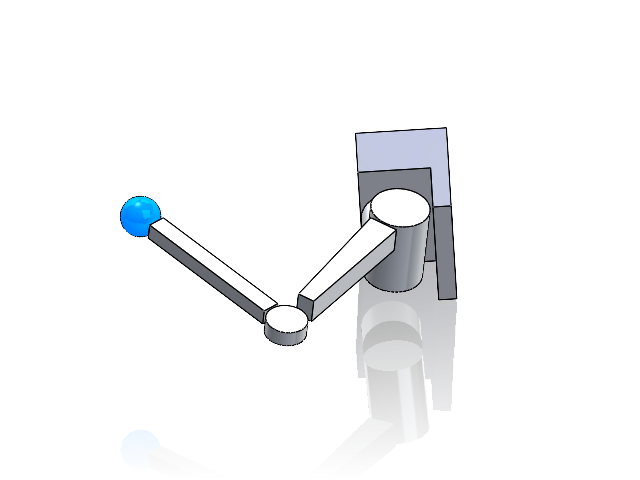
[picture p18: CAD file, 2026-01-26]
Hardware/Mechanics/시뮬/어셈블리.SLDASM
Calf_mesh
foot_mesh
Hip_motor
Thigh_calf_motor
Thigh_mesh
knee_joint
platform

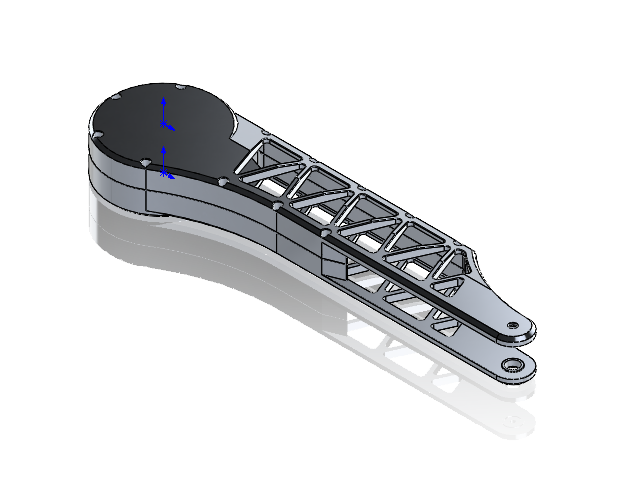
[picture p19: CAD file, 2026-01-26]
Hardware/Mechanics/4족 3D/허벅지 일체형.SLDASM
thigh(1) - 2
thigh(2) - 2

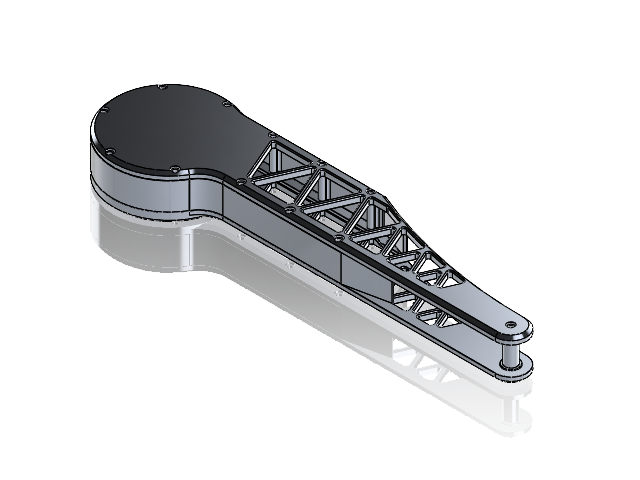
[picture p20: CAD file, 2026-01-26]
Hardware/Mechanics/4족 3D/허벅지.SLDASM
thigh(1) - 3-1
thigh(1) - 3-2
thigh(1) - 3-3
thigh(1) - 3-4
thigh(1) - 3-5
calf_thigh_I

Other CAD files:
Hardware/Mechanics/4족 3D/W678AZZ.sldasm
Hardware/Mechanics/4족 3D/3mf/hip_calf_jig.gcode.3mf
Hardware/Mechanics/4족 3D/DWG 도면/link.DWG
Hardware/Mechanics/thigh_link_BB.dwg
Hardware/Mechanics/4족 3D/DWG 도면/calf_link_ll.DWG
Hardware/Mechanics/4족 3D/2D 도면/calf_1_1.SLDDRW
Hardware/Mechanics/4족 3D/2D 도면/calf_1_2.SLDDRW
Hardware/Mechanics/4족 3D/2D 도면/calf_link_l.SLDDRW
Hardware/Mechanics/4족 3D/2D 도면/calf_link_ll.SLDDRW
Hardware/Mechanics/4족 3D/2D 도면/calf_thigh_I.SLDDRW
Hardware/Mechanics/4족 3D/2D 도면/connector_1.SLDDRW
Hardware/Mechanics/4족 3D/2D 도면/connector_2.SLDDRW
Hardware/Mechanics/4족 3D/2D 도면/foot_cover_1.SLDDRW
Hardware/Mechanics/4족 3D/2D 도면/foot_cover_2.SLDDRW
Hardware/Mechanics/4족 3D/2D 도면/hip_calf_jig_2.SLDDRW
Hardware/Mechanics/4족 3D/2D 도면/hip_stopper.SLDDRW
Hardware/Mechanics/4족 3D/2D 도면/hip_thigh_2.SLDDRW
Hardware/Mechanics/4족 3D/2D 도면/link.SLDDRW
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

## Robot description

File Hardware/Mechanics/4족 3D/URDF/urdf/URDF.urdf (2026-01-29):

<?xml version="1.0" encoding="utf-8"?>
<!-- This URDF was automatically created by SolidWorks to URDF Exporter! Originally created by Stephen Brawner (brawner@gmail.com) 
     Commit Version: 1.6.0-4-g7f85cfe  Build Version: 1.6.7995.38578
     For more information, please see http://wiki.ros.org/sw_urdf_exporter -->
<robot name="URDF">
  <link name="Base_link">
    <inertial>
      <origin xyz="0.12824 0.038225 0.045584" rpy="0 0 0" />
      <mass value="2.20928" />
      <inertia ixx="0.0080598" ixy="-5.7974E-06" ixz="-2.1256E-06" iyy="0.0039704" iyz="2.6662E-05" izz="0.0055375" />
    </inertial>
    <visual>
      <origin xyz="0 0 0" rpy="0 0 0" />
      <geometry>
        <mesh filename="package://URDF/meshes/Base_link.STL" />
      </geometry>
      <material name="">
        <color rgba="0.75294 0.75294 0.75294 1" />
      </material>
    </visual>
    <collision>
      <origin xyz="0 0 0" rpy="0 0 0" />
      <geometry>
        <mesh filename="package://URDF/meshes/Base_link.STL" />
      </geometry>
    </collision>
  </link>
  <link name="Hip_link">
    <inertial>
      <origin xyz="0.00034503 -0.013108 0.044177" rpy="0 0 0" />
      <mass value="1.008" />
      <inertia ixx="8.916E-05" ixy="-6.9168E-08" ixz="-4.6352E-06" iyy="0.00018713" iyz="-3.0023E-08" izz="0.00011382" />
    </inertial>
    <visual>
      <origin xyz="0 0 0" rpy="0 0 0" />
      <geometry>
        <mesh filename="package://URDF/meshes/Hip_link.STL" />
      </geometry>
      <material name="">
        <color rgba="0.75294 0.75294 0.75294 1" />
      </material>
    </visual>
    <collision>
      <origin xyz="0 0 0" rpy="0 0 0" />
      <geometry>
        <mesh filename="package://URDF/meshes/Hip_link.STL" />
      </geometry>
    </collision>
  </link>
  <joint name="Hip_joint" type="revolute">
    <origin xyz="0 0 0" rpy="0 0 0" />
    <parent link="Base_link" />
    <child link="Hip_link" />
    <axis xyz="0 0 -1" />
    <limit lower="0.1309" upper="3.0107" effort="0" velocity="0" />
  </joint>
  <link name="Thigh_link">
    <inertial>
      <origin xyz="-0.091961 0.075591 0.0076548" rpy="0 0 0" />
      <mass value="2.0083" />
      <inertia ixx="0.00082748" ixy="1.7039E-05" ixz="0.00024101" iyy="0.012827" iyz="1.1342E-06" izz="0.012075" />
    </inertial>
    <visual>
      <origin xyz="0 0 0" rpy="0 0 0" />
      <geometry>
        <mesh filename="package://URDF/meshes/Thigh_link.STL" />
      </geometry>
      <material name="">
        <color rgba="0.75294 0.75294 0.75294 1" />
      </material>
    </visual>
    <collision>
      <origin xyz="0 0 0" rpy="0 0 0" />
      <geometry>
        <mesh filename="package://URDF/meshes/Thigh_link.STL" />
      </geometry>
    </collision>
  </link>
  <joint name="Thigh_joint" type="revolute">
    <origin xyz="0 0.0082 0.058" rpy="0 0 0" />
    <parent link="Hip_link" />
    <child link="Thigh_link" />
    <axis xyz="0 -1 0" />
    <limit lower="0.1571" upper="6.1359" effort="0" velocity="0" />
  </joint>
  <link name="Calf_link">
    <inertial>
      <origin xyz="-0.15293 -0.00023583 -0.011724" rpy="0 0 0" />
      <mass value="0.53382" />
      <inertia ixx="0.00016402" ixy="-3.6853E-10" ixz="-0.00042607" iyy="0.0076992" iyz="2.8095E-10" izz="0.0075849" />
    </inertial>
    <visual>
      <origin xyz="0 0 0" rpy="0 0 0" />
      <geometry>
        <mesh filename="package://URDF/meshes/Calf_link.STL" />
      </geometry>
      <material name="">
        <color rgba="0.75294 0.75294 0.75294 1" />
      </material>
    </visual>
    <collision>
      <origin xyz="0 0 0" rpy="0 0 0" />
      <geometry>
        <mesh filename="package://URDF/meshes/Calf_link.STL" />
      </geometry>
    </collision>
  </link>
  <joint name="Calf_joint" type="revolute">
    <origin xyz="-0.35 0.089 0" rpy="0 0 0" />
    <parent link="Thigh_link" />
    <child link="Calf_link" />
    <axis xyz="0 -1 0" />
    <limit lower="0.3801" upper="2.5831" effort="0" velocity="0" />
  </joint>
  <link name="Foot">
    <inertial>
      <origin xyz="0.19707 -0.00023583 -0.011724" rpy="0 0 0" />
      <mass value="0.53382" />
      <inertia ixx="0.00016402" ixy="-3.6853E-10" ixz="-0.00042607" iyy="0.0076992" iyz="2.8095E-10" izz="0.0075849" />
    </inertial>
    <visual>
      <origin xyz="0 0 0" rpy="0 0 0" />
      <geometry>
        <mesh filename="package://URDF/meshes/Foot.STL" />
      </geometry>
      <material name="">
        <color rgba="0.75294 0.75294 0.75294 1" />
      </material>
    </visual>
    <collision>
      <origin xyz="0 0 0" rpy="0 0 0" />
      <geometry>
        <mesh filename="package://URDF/meshes/Foot.STL" />
      </geometry>
    </collision>
  </link>
  <joint name="Foot_point" type="fixed">
    <origin xyz="-0.35 0 0" rpy="0 0 0" />
    <parent link="Calf_link" />
    <child link="Foot" />
    <axis xyz="0 0 0" />
  </joint>
</robot>

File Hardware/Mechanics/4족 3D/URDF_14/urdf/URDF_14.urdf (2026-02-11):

<?xml version="1.0" encoding="utf-8"?>
<!-- This URDF was automatically created by SolidWorks to URDF Exporter! Originally created by Stephen Brawner (brawner@gmail.com) 
     Commit Version: 1.6.0-4-g7f85cfe  Build Version: 1.6.7995.38578
     For more information, please see http://wiki.ros.org/sw_urdf_exporter -->
<robot name="URDF_14">
  <link name="base_link">
    <inertial>
      <origin xyz="-0.038225 -0.045584 0.12824" rpy="0 0 0" />
      <mass value="2.2093" />
      <inertia ixx="0.0039704" ixy="2.6662E-05" ixz="5.7974E-06" iyy="0.0055375" iyz="2.1256E-06" izz="0.0080598" />
    </inertial>
    <visual>
      <origin xyz="0 0 0" rpy="0 0 0" />
      <geometry>
        <mesh filename="package://URDF_14/meshes/base_link.STL" />
      </geometry>
      <material name="">
        <color rgba="0.75294 0.75294 0.75294 1" />
      </material>
    </visual>
    <collision>
      <origin xyz="0 0 0" rpy="0 0 0" />
      <geometry>
        <mesh filename="package://URDF_14/meshes/base_link.STL" />
      </geometry>
    </collision>
  </link>
  <link name="Hip_link">
    <inertial>
      <origin xyz="0.013108 -0.044177 0.00034503" rpy="0 0 0" />
      <mass value="1.008" />
      <inertia ixx="0.00018713" ixy="-3.0023E-08" ixz="6.9168E-08" iyy="0.00011382" iyz="4.6352E-06" izz="8.916E-05" />
    </inertial>
    <visual>
      <origin xyz="0 0 0" rpy="0 0 0" />
      <geometry>
        <mesh filename="package://URDF_14/meshes/Hip_link.STL" />
      </geometry>
      <material name="">
        <color rgba="0.75294 0.75294 0.75294 1" />
      </material>
    </visual>
    <collision>
      <origin xyz="0 0 0" rpy="0 0 0" />
      <geometry>
        <mesh filename="package://URDF_14/meshes/Hip_link.STL" />
      </geometry>
    </collision>
  </link>
  <joint name="Hip" type="revolute">
    <origin xyz="0 0 0" rpy="0 0 0" />
    <parent link="base_link" />
    <child link="Hip_link" />
    <axis xyz="0 1 0" />
    <limit lower="-1.4399" upper="1.4399" effort="0" velocity="0" />
  </joint>
  <link name="Thigh_link">
    <inertial>
      <origin xyz="-0.075591 -0.0076549 -0.091964" rpy="0 0 0" />
      <mass value="2.00827" />
      <inertia ixx="0.012828" ixy="1.1342E-06" ixz="-1.7039E-05" iyy="0.012075" iyz="-0.00024099" izz="0.00082748" />
    </inertial>
    <visual>
      <origin xyz="0 0 0" rpy="0 0 0" />
      <geometry>
        <mesh filename="package://URDF_14/meshes/Thigh_link.STL" />
      </geometry>
      <material name="">
        <color rgba="0.75294 0.75294 0.75294 1" />
      </material>
    </visual>
    <collision>
      <origin xyz="0 0 0" rpy="0 0 0" />
      <geometry>
        <mesh filename="package://URDF_14/meshes/Thigh_link.STL" />
      </geometry>
    </collision>
  </link>
  <joint name="Thigh" type="revolute">
    <origin xyz="-0.0082 -0.058 0" rpy="0 0 0" />
    <parent link="Hip_link" />
    <child link="Thigh_link" />
    <axis xyz="1 0 0" />
    <limit lower="-2.9845" upper="2.9845" effort="0" velocity="0" />
  </joint>
  <link name="Calf_link">
    <inertial>
      <origin xyz="0.000203770717243083 0.00952938812029318 -0.176982427275814" rpy="0 0 0" />
      <mass value="0.60518433734649" />
      <inertia ixx="0.00772794484997601" ixy="1.44224271129486E-08" ixz="1.45933169504129E-08" iyy="0.00760727594236918" iyz="0.000432410282188059" izz="0.00018638549348508" />
    </inertial>
    <visual>
      <origin xyz="0 0 0" rpy="0 0 0" />
      <geometry>
        <mesh filename="package://URDF_14/meshes/Calf_link.STL" />
      </geometry>
      <material name="">
        <color rgba="0.792156862745098 0.819607843137255 0.933333333333333 1" />
      </material>
    </visual>
    <collision>
      <origin xyz="0 0 0" rpy="0 0 0" />
      <geometry>
        <mesh filename="package://URDF_14/meshes/Calf_link.STL" />
      </geometry>
    </collision>
  </link>
  <joint name="Calf" type="revolute">
    <origin xyz="-0.089 0 -0.35" rpy="0 0 0" />
    <parent link="Thigh_link" />
    <child link="Calf_link" />
    <axis xyz="1 0 0" />
    <limit lower="0.294" upper="2.793" effort="0" velocity="0" />
  </joint>
</robot>

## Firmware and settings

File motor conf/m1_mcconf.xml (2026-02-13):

<?xml version="1.0" encoding="UTF-8"?>
<MCConfiguration>
  <pwm_mode>1</pwm_mode>
  <comm_mode>0</comm_mode>
  <motor_type>2</motor_type>
  <sensor_mode>0</sensor_mode>
  <l_current_max>28.617928</l_current_max>
  <l_current_min>-28.617928</l_current_min>
  <l_in_current_max>99.000000</l_in_current_max>
  <l_in_current_min>-60.000000</l_in_current_min>
  <l_abs_current_max>80.000000</l_abs_current_max>
  <l_min_erpm>-100000.000000</l_min_erpm>
  <l_max_erpm>100000.000000</l_max_erpm>
  <l_erpm_start>0.800000</l_erpm_start>
  <l_max_erpm_fbrake>300.000000</l_max_erpm_fbrake>
  <l_max_erpm_fbrake_cc>1500.000000</l_max_erpm_fbrake_cc>
  <l_min_vin>8.000000</l_min_vin>
  <l_max_vin>57.000000</l_max_vin>
  <l_battery_cut_start>10.000000</l_battery_cut_start>
  <l_battery_cut_end>8.000000</l_battery_cut_end>
  <l_slow_abs_current>1</l_slow_abs_current>
  <l_temp_fet_start>85.000000</l_temp_fet_start>
  <l_temp_fet_end>100.000000</l_temp_fet_end>
  <l_temp_motor_start>105.000000</l_temp_motor_start>
  <l_temp_motor_end>110.000000</l_temp_motor_end>
  <l_temp_accel_dec>0.150000</l_temp_accel_dec>
  <l_min_duty>0.000000</l_min_duty>
  <l_max_duty>0.950000</l_max_duty>
  <l_watt_max>1500000.000000</l_watt_max>
  <l_watt_min>-1500000.000000</l_watt_min>
  <l_current_max_scale>1.000000</l_current_max_scale>
  <l_current_min_scale>1.000000</l_current_min_scale>
  <l_duty_start>1.000000</l_duty_start>
  <sl_min_erpm>150.000000</sl_min_erpm>
  <sl_min_erpm_cycle_int_limit>1100.000000</sl_min_erpm_cycle_int_limit>
  <sl_max_fullbreak_current_dir_change>10.000000</sl_max_fullbreak_current_dir_change>
  <sl_cycle_int_limit>62.000000</sl_cycle_int_limit>
  <sl_phase_advance_at_br>0.800000</sl_phase_advance_at_br>
  <sl_cycle_int_rpm_br>80000.000000</sl_cycle_int_rpm_br>
  <sl_bemf_coupling_k>600.000000</sl_bemf_coupling_k>
  <hall_table_0>255</hall_table_0>
  <hall_table_1>1</hall_table_1>
  <hall_table_2>3</hall_table_2>
  <hall_table_3>2</hall_table_3>
  <hall_table_4>5</hall_table_4>
  <hall_table_5>6</hall_table_5>
  <hall_table_6>4</hall_table_6>
  <hall_table_7>255</hall_table_7>
  <hall_sl_erpm>2000.000000</hall_sl_erpm>
  <foc_current_kp>0.026416</foc_current_kp>
  <foc_current_ki>61.051121</foc_current_ki>
  <foc_f_sw>25000.000000</foc_f_sw>
  <foc_dt_us>0.120000</foc_dt_us>
  <foc_encoder_inverted>1</foc_encoder_inverted>
  <foc_encoder_offset>162.270432</foc_encoder_offset>
  <foc_encoder_ratio>21.000000</foc_encoder_ratio>
  <foc_encoder_sin_gain>1.000000</foc_encoder_sin_gain>
  <foc_encoder_cos_gain>1.000000</foc_encoder_cos_gain>
  <foc_encoder_sin_offset>1.650000</foc_encoder_sin_offset>
  <foc_encoder_cos_offset>1.650000</foc_encoder_cos_offset>
  <foc_encoder_sincos_filter_constant>0.500000</foc_encoder_sincos_filter_constant>
  <foc_sensor_mode>1</foc_sensor_mode>
  <foc_pll_kp>2000.000000</foc_pll_kp>
  <foc_pll_ki>30000.000000</foc_pll_ki>
  <foc_motor_l>0.000026</foc_motor_l>
  <foc_motor_ld_lq_diff>0.000000</foc_motor_ld_lq_diff>
  <foc_motor_r>0.061051</foc_motor_r>
  <foc_motor_flux_linkage>0.004558</foc_motor_flux_linkage>
  <foc_observer_gain>48136012.000000</foc_observer_gain>
  <foc_observer_gain_slow>0.050000</foc_observer_gain_slow>
  <foc_duty_dowmramp_kp>10.000000</foc_duty_dowmramp_kp>
  <foc_duty_dowmramp_ki>200.000000</foc_duty_dowmramp_ki>
  <foc_openloop_rpm>1500.000000</foc_openloop_rpm>
  <foc_openloop_rpm_low>0.000000</foc_openloop_rpm_low>
  <foc_d_gain_scale_start>0.900000</foc_d_gain_scale_start>
  <foc_d_gain_scale_max_mod>0.200000</foc_d_gain_scale_max_mod>
  <foc_sl_openloop_hyst>0.100000</foc_sl_openloop_hyst>
  <foc_sl_openloop_time_lock>0.000000</foc_sl_openloop_time_lock>
  <foc_sl_openloop_time_ramp>0.100000</foc_sl_openloop_time_ramp>
  <foc_sl_openloop_time>0.050000</foc_sl_openloop_time>
  <foc_hall_table_0>255</foc_hall_table_0>
  <foc_hall_table_1>255</foc_hall_table_1>
  <foc_hall_table_2>255</foc_hall_table_2>
  <foc_hall_table_3>255</foc_hall_table_3>
  <foc_hall_table_4>255</foc_hall_table_4>
  <foc_hall_table_5>255</foc_hall_table_5>
  <foc_hall_table_6>255</foc_hall_table_6>
  <foc_hall_table_7>255</foc_hall_table_7>
  <foc_hall_interp_erpm>500.000000</foc_hall_interp_erpm>
  <foc_sl_erpm>2500.000000</foc_sl_erpm>
  <foc_sample_v0_v7>0</foc_sample_v0_v7>
  <foc_sample_high_current>0</foc_sample_high_current>
  <foc_sat_comp>0.000000</foc_sat_comp>
  <foc_temp_comp>0</foc_temp_comp>
  <foc_temp_comp_base_temp>25.000000</foc_temp_comp_base_temp>
  <foc_current_filter_const>0.100000</foc_current_filter_const>
  <foc_cc_decoupling>2</foc_cc_decoupling>
  <foc_observer_type>0</foc_observer_type>
  <foc_hfi_voltage_start>20.000000</foc_hfi_voltage_start>
  <foc_hfi_voltage_run>4.000000</foc_hfi_voltage_run>
  <foc_hfi_voltage_max>10.000000</foc_hfi_voltage_max>
  <foc_sl_erpm_hfi>2000.000000</foc_sl_erpm_hfi>
  <foc_hfi_start_samples>65</foc_hfi_start_samples>
  <foc_hfi_obs_ovr_sec>0.001000</foc_hfi_obs_ovr_sec>
  <foc_hfi_samples>1</foc_hfi_samples>
  <gpd_buffer_notify_left>200</gpd_buffer_notify_left>
  <gpd_buffer_interpol>0</gpd_buffer_interpol>
  <gpd_current_filter_const>0.100000</gpd_current_filter_const>
  <gpd_current_kp>0.030000</gpd_current_kp>
  <gpd_current_ki>50.000000</gpd_current_ki>
  <s_pid_kp>0.004000</s_pid_kp>
  <s_pid_ki>0.004000</s_pid_ki>
  <s_pid_kd>0.000100</s_pid_kd>
  <s_pid_kd_filter>0.900000</s_pid_kd_filter>
  <s_pid_min_erpm>300.000000</s_pid_min_erpm>
  <s_pid_allow_braking>1</s_pid_allow_braking>
  <s_pid_ramp_erpms_s>50000.000000</s_pid_ramp_erpms_s>
  <p_pid_kp>0.018000</p_pid_kp>
  <p_pid_ki>0.000000</p_pid_ki>
  <p_pid_kd>0.000320</p_pid_kd>
  <p_pid_kd_filter>0.200000</p_pid_kd_filter>
  <p_pid_ang_div>1.000000</p_pid_ang_div>
  <cc_startup_boost_duty>0.010000</cc_startup_boost_duty>
  <cc_min_current>0.050000</cc_min_current>
  <cc_gain>0.004600</cc_gain>
  <cc_ramp_step_max>0.040000</cc_ramp_step_max>
  <m_fault_stop_time_ms>500</m_fault_stop_time_ms>
  <m_duty_ramp_step>0.020000</m_duty_ramp_step>
  <m_current_backoff_gain>0.500000</m_current_backoff_gain>
  <m_encoder_counts>8192</m_encoder_counts>
  <m_sensor_port_mode>7</m_sensor_port_mode>
  <m_invert_direction>0</m_invert_direction>
  <m_drv8301_oc_mode>0</m_drv8301_oc_mode>
  <m_drv8301_oc_adj>16</m_drv8301_oc_adj>
  <m_bldc_f_sw_min>3000.000000</m_bldc_f_sw_min>
  <m_bldc_f_sw_max>35000.000000</m_bldc_f_sw_max>
  <m_dc_f_sw>25000.000000</m_dc_f_sw>
  <m_ntc_motor_beta>3380.000000</m_ntc_motor_beta>
  <m_out_aux_mode>0</m_out_aux_mode>
  <m_motor_temp_sens_type>0</m_motor_temp_sens_type>
  <m_ptc_motor_coeff>0.610000</m_ptc_motor_coeff>
  <m_hall_extra_samples>1</m_hall_extra_samples>
  <si_motor_poles>14</si_motor_poles>
  <si_gear_ratio>3.000000</si_gear_ratio>
  <si_wheel_diameter>0.083000</si_wheel_diameter>
  <si_battery_type>0</si_battery_type>
  <si_battery_cells>3</si_battery_cells>
  <si_battery_ah>6.000000</si_battery_ah>
  <bms.type>1</bms.type>
  <bms.t_limit_start>45.000000</bms.t_limit_start>
  <bms.t_limit_end>65.000000</bms.t_limit_end>
  <bms.soc_limit_start>0.050000</bms.soc_limit_start>
  <bms.soc_limit_end>0.000000</bms.soc_limit_end>
</MCConfiguration>

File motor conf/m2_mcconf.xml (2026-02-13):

<?xml version="1.0" encoding="UTF-8"?>
<APPConfiguration>
  <controller_id>2</controller_id>
  <timeout_msec>1000</timeout_msec>
  <timeout_brake_current>0.000000</timeout_brake_current>
  <send_can_status>4</send_can_status>
  <send_can_status_rate_hz>100</send_can_status_rate_hz>
  <can_baud_rate>3</can_baud_rate>
  <pairing_done>0</pairing_done>
  <permanent_uart_enabled>1</permanent_uart_enabled>
  <shutdown_mode>7</shutdown_mode>
  <can_mode>0</can_mode>
  <uavcan_esc_index>0</uavcan_esc_index>
  <uavcan_raw_mode>0</uavcan_raw_mode>
  <app_to_use>8</app_to_use>
  <app_ppm_conf.ctrl_type>0</app_ppm_conf.ctrl_type>
  <app_ppm_conf.pid_max_erpm>15000.000000</app_ppm_conf.pid_max_erpm>
  <app_ppm_conf.hyst>0.150000</app_ppm_conf.hyst>
  <app_ppm_conf.pulse_start>1.000000</app_ppm_conf.pulse_start>
  <app_ppm_conf.pulse_end>2.000000</app_ppm_conf.pulse_end>
  <app_ppm_conf.pulse_center>1.500000</app_ppm_conf.pulse_center>
  <app_ppm_conf.median_filter>1</app_ppm_conf.median_filter>
  <app_ppm_conf.safe_start>1</app_ppm_conf.safe_start>
  <app_ppm_conf.throttle_exp>0.000000</app_ppm_conf.throttle_exp>
  <app_ppm_conf.throttle_exp_brake>0.000000</app_ppm_conf.throttle_exp_brake>
  <app_ppm_conf.throttle_exp_mode>2</app_ppm_conf.throttle_exp_mode>
  <app_ppm_conf.ramp_time_pos>0.400000</app_ppm_conf.ramp_time_pos>
  <app_ppm_conf.ramp_time_neg>0.200000</app_ppm_conf.ramp_time_neg>
  <app_ppm_conf.multi_esc>1</app_ppm_conf.multi_esc>
  <app_ppm_conf.tc>0</app_ppm_conf.tc>
  <app_ppm_conf.tc_max_diff>3000.000000</app_ppm_conf.tc_max_diff>
  <app_ppm_conf.max_erpm_for_dir>4000.000000</app_ppm_conf.max_erpm_for_dir>
  <app_ppm_conf.smart_rev_max_duty>0.070000</app_ppm_conf.smart_rev_max_duty>
  <app_ppm_conf.smart_rev_ramp_time>3.000000</app_ppm_conf.smart_rev_ramp_time>
  <app_adc_conf.ctrl_type>0</app_adc_conf.ctrl_type>
  <app_adc_conf.hyst>0.150000</app_adc_conf.hyst>
  <app_adc_conf.voltage_start>0.900000</app_adc_conf.voltage_start>
  <app_adc_conf.voltage_end>3.000000</app_adc_conf.voltage_end>
  <app_adc_conf.voltage_center>2.000000</app_adc_conf.voltage_center>
  <app_adc_conf.voltage2_start>0.900000</app_adc_conf.voltage2_start>
  <app_adc_conf.voltage2_end>3.000000</app_adc_conf.voltage2_end>
  <app_adc_conf.use_filter>1</app_adc_conf.use_filter>
  <app_adc_conf.safe_start>1</app_adc_conf.safe_start>
  <app_adc_conf.cc_button_inverted>0</app_adc_conf.cc_button_inverted>
  <app_adc_conf.rev_button_inverted>0</app_adc_conf.rev_button_inverted>
  <app_adc_conf.voltage_inverted>0</app_adc_conf.voltage_inverted>
  <app_adc_conf.voltage2_inverted>0</app_adc_conf.voltage2_inverted>
  <app_adc_conf.throttle_exp>0.000000</app_adc_conf.throttle_exp>
  <app_adc_conf.throttle_exp_brake>0.000000</app_adc_conf.throttle_exp_brake>
  <app_adc_conf.throttle_exp_mode>2</app_adc_conf.throttle_exp_mode>
  <app_adc_conf.ramp_time_pos>0.300000</app_adc_conf.ramp_time_pos>
  <app_adc_conf.ramp_time_neg>0.100000</app_adc_conf.ramp_time_neg>
  <app_adc_conf.multi_esc>1</app_adc_conf.multi_esc>
  <app_adc_conf.tc>0</app_adc_conf.tc>
  <app_adc_conf.tc_max_diff>3000.000000</app_adc_conf.tc_max_diff>
  <app_adc_conf.update_rate_hz>500</app_adc_conf.update_rate_hz>
  <app_uart_baudrate>115200</app_uart_baudrate>
  <app_chuk_conf.ctrl_type>1</app_chuk_conf.ctrl_type>
  <app_chuk_conf.hyst>0.150000</app_chuk_conf.hyst>
  <app_chuk_conf.ramp_time_pos>0.400000</app_chuk_conf.ramp_time_pos>
  <app_chuk_conf.ramp_time_neg>0.200000</app_chuk_conf.ramp_time_neg>
  <app_chuk_conf.stick_erpm_per_s_in_cc>3000.000000</app_chuk_conf.stick_erpm_per_s_in_cc>
  <app_chuk_conf.throttle_exp>0.000000</app_chuk_conf.throttle_exp>
  <app_chuk_conf.throttle_exp_brake>0.000000</app_chuk_conf.throttle_exp_brake>
  <app_chuk_conf.throttle_exp_mode>2</app_chuk_conf.throttle_exp_mode>
  <app_chuk_conf.multi_esc>1</app_chuk_conf.multi_esc>
  <app_chuk_conf.tc>0</app_chuk_conf.tc>
  <app_chuk_conf.tc_max_diff>3000.000000</app_chuk_conf.tc_max_diff>
  <app_chuk_conf.use_smart_rev>1</app_chuk_conf.use_smart_rev>
  <app_chuk_conf.smart_rev_max_duty>0.070000</app_chuk_conf.smart_rev_max_duty>
  <app_chuk_conf.smart_rev_ramp_time>3.000000</app_chuk_conf.smart_rev_ramp_time>
  <app_nrf_conf.speed>1</app_nrf_conf.speed>
  <app_nrf_conf.power>3</app_nrf_conf.power>
  <app_nrf_conf.crc_type>1</app_nrf_conf.crc_type>
  <app_nrf_conf.retry_delay>0</app_nrf_conf.retry_delay>
  <app_nrf_conf.retries>3</app_nrf_conf.retries>
  <app_nrf_conf.channel>76</app_nrf_conf.channel>
  <app_nrf_conf.address_0>198</app_nrf_conf.address_0>
  <app_nrf_conf.address_1>199</app_nrf_conf.address_1>
  <app_nrf_conf.address_2>0</app_nrf_conf.address_2>
  <app_nrf_conf.send_crc_ack>1</app_nrf_conf.send_crc_ack>
  <app_balance_conf.kp>0.000000</app_balance_conf.kp>
  <app_balance_conf.ki>0.000000</app_balance_conf.ki>
  <app_balance_conf.kd>0.000000</app_balance_conf.kd>
  <app_balance_conf.hertz>1000</app_balance_conf.hertz>
  <app_balance_conf.fault_pitch>20.000000</app_balance_conf.fault_pitch>
  <app_balance_conf.fault_roll>45.000000</app_balance_conf.fault_roll>
  <app_balance_conf.fault_duty>0.900000</app_balance_conf.fault_duty>
  <app_balance_conf.fault_adc1>0.000000</app_balance_conf.fault_adc1>
  <app_balance_conf.fault_adc2>0.000000</app_balance_conf.fault_adc2>
  <app_balance_conf.fault_delay_pitch>0</app_balance_conf.fault_delay_pitch>
  <app_balance_conf.fault_delay_roll>0</app_balance_conf.fault_delay_roll>
  <app_balance_conf.fault_delay_duty>0</app_balance_conf.fault_delay_duty>
  <app_balance_conf.fault_delay_switch_half>0</app_balance_conf.fault_delay_switch_half>
  <app_balance_conf.fault_delay_switch_full>0</app_balance_conf.fault_delay_switch_full>
  <app_balance_conf.fault_adc_half_erpm>1000</app_balance_conf.fault_adc_half_erpm>
  <app_balance_conf.tiltback_angle>15.000000</app_balance_conf.tiltback_angle>
  <app_balance_conf.tiltback_speed>5.000000</app_balance_conf.tiltback_speed>
  <app_balance_conf.tiltback_duty>0.750000</app_balance_conf.tiltback_duty>
  <app_balance_conf.tiltback_high_voltage>200.000000</app_balance_conf.tiltback_high_voltage>
  <app_balance_conf.tiltback_low_voltage>0.000000</app_balance_conf.tiltback_low_voltage>
  <app_balance_conf.tiltback_constant>0.000000</app_balance_conf.tiltback_constant>
  <app_balance_conf.tiltback_constant_erpm>500</app_balance_conf.tiltback_constant_erpm>
  <app_balance_conf.startup_pitch_tolerance>20.000000</app_balance_conf.startup_pitch_tolerance>
  <app_balance_conf.startup_roll_tolerance>8.000000</app_balance_conf.startup_roll_tolerance>
  <app_balance_conf.startup_speed>30.000000</app_balance_conf.startup_speed>
  <app_balance_conf.deadzone>0.000000</app_balance_conf.deadzone>
  <app_balance_conf.current_boost>0.000000</app_balance_conf.current_boost>
  <app_balance_conf.multi_esc>0</app_balance_conf.multi_esc>
  <app_balance_conf.yaw_kp>0.000000</app_balance_conf.yaw_kp>
  <app_balance_conf.yaw_ki>0.000000</app_balance_conf.yaw_ki>
  <app_balance_conf.yaw_kd>0.000000</app_balance_conf.yaw_kd>
  <app_balance_conf.roll_steer_kp>0.000000</app_balance_conf.roll_steer_kp>
  <app_balance_conf.roll_steer_erpm_kp>0.000000</app_balance_conf.roll_steer_erpm_kp>
  <app_balance_conf.brake_current>0.000000</app_balance_conf.brake_current>
  <app_balance_conf.yaw_current_clamp>0.000000</app_balance_conf.yaw_current_clamp>
  <app_balance_conf.setpoint_pitch_filter>0.000000</app_balance_conf.setpoint_pitch_filter>
  <app_balance_conf.setpoint_target_filter>1.000000</app_balance_conf.setpoint_target_filter>
  <app_balance_conf.setpoint_filter_clamp>8.000000</app_balance_conf.setpoint_filter_clamp>
  <app_balance_conf.kd_pt1_frequency>0</app_balance_conf.kd_pt1_frequency>
  <app_pas_conf.ctrl_type>0</app_pas_conf.ctrl_type>
  <app_pas_conf.sensor_type>0</app_pas_conf.sensor_type>
  <app_pas_conf.current_scaling>0.100000</app_pas_conf.current_scaling>
  <app_pas_conf.pedal_rpm_start>10.000000</app_pas_conf.pedal_rpm_start>
  <app_pas_conf.pedal_rpm_end>180.000000</app_pas_conf.pedal_rpm_end>
  <app_pas_conf.invert_pedal_direction>0</app_pas_conf.invert_pedal_direction>
  <app_pas_conf.magnets>24</app_pas_conf.magnets>
  <app_pas_conf.use_filter>1</app_pas_conf.use_filter>
  <app_pas_conf.ramp_time_pos>0.600000</app_pas_conf.ramp_time_pos>
  <app_pas_conf.ramp_time_neg>0.300000</app_pas_conf.ramp_time_neg>
  <app_pas_conf.update_rate_hz>500</app_pas_conf.update_rate_hz>
  <imu_conf.type>1</imu_conf.type>
  <imu_conf.mode>0</imu_conf.mode>
  <imu_conf.sample_rate_hz>200</imu_conf.sample_rate_hz>
  <imu_conf.accel_confidence_decay>1.000000</imu_conf.accel_confidence_decay>
  <imu_conf.mahony_kp>0.300000</imu_conf.mahony_kp>
  <imu_conf.mahony_ki>0.000000</imu_conf.mahony_ki>
  <imu_conf.madgwick_beta>0.100000</imu_conf.madgwick_beta>
  <imu_conf.rot_roll>0.000000</imu_conf.rot_roll>
  <imu_conf.rot_pitch>0.000000</imu_conf.rot_pitch>
  <imu_conf.rot_yaw>0.000000</imu_conf.rot_yaw>
  <imu_conf.accel_offsets_0>0.000000</imu_conf.accel_offsets_0>
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

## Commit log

2026-01-26 file upload
    [4족로봇 정보.xlsx, AJPNGLB3-P4-B3-G3-ML4.SLDPRT, AK10-9 V2-0.stp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]
2026-01-29 files update
    [Calf_link.SLDASM, URDF.csv, URDF.urdf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]
2026-02-13 pdf 커밋
    pdf 커밋
    [m1_mcconf.xml, m2_mcconf.xml, 지출관리.xlsx]
